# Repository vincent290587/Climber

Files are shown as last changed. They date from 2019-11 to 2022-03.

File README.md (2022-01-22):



# Project

This is another project of an indoor-trainer grade simulator.  
It is meant to be used with Zwift, but could be used with any other similar program or game.  
The concept was inspired by the Wahoo Kickr Climb, but with different strategy / parts !

- [x] Sensors readout
- [x] ANT+ FE-C Slope sniffing
- [x] Kalman filtering
- [x] Actuator command
- [x] User params flash saving
- [x] Zwift TCP packets sniffing for ERG (or any) mode slope sniffing.

<p align="center">
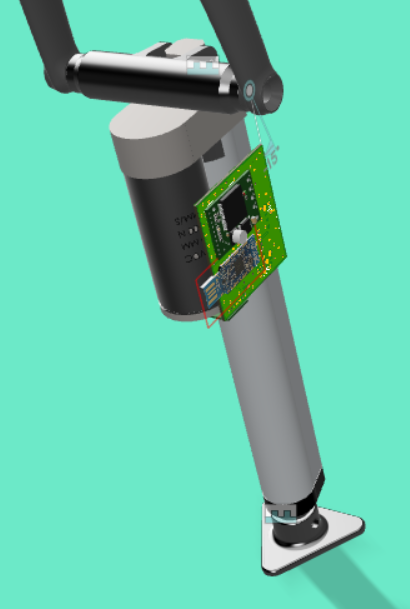
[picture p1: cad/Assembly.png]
Assembly

</p>

# Concept

The ANT+ target incline is sniffed using the ANT+ protocol, it is then compared to the filtered measured front wheel hub height.  
Two 3D printed parts (in the CAD folder) allow to mount securely the actuator to the bike's fork, and to the ground.  
You know the rest ;-)

## Slope detection

The software can work in 2 modes:  
- The slope is sniffed in Zwift TCP packets directly (preferred, but only works with Zwift...),  
- or it can be obtained from the game ANT+ packets (only works in simulation mode and not in ERG...).

So... pick your poison !

## Incline achievement

The current bike front wheel hub's height is computed using a ToF infrared laser sensor: the VL53L1x.  
These measurement are input in a Kalman filter to get a better dynamic estimate of the bike's incline.  
A VNH5019 is then PWMed to drive the linear actuator.

# Hardware

- MCU: nRF52840 (BLE and ANT+), in the form of the PCA10059 (USB dongle) from Nordic
- Incline detection: ToF laser sensor VL53L1x (Pololu)
- Motor controller: VNH5019 (Pololu)

# How to use it ?

## Hardware connections

The pinout that is used is defined in the file named `custom_board_v1.h`.  

Eagle PCB files:

https://github.com/vincent290587/EAGLE/tree/master/Projects/Climber

## Pre-compiled files

See folder /hex.

## Pre-requisites

Download the nRF52 SDK from Nordic:  
https://www.nordicsemi.com/Products/Development-software/nRF5-SDK/Download?lang=en#infotabs  

Decompress it somewhere and write down that location (needed to go in the compil/s340/Makefile.local).

If you choose to use the ANT+ mode you'll have to install the ANT+ keys in that SDK. (follow Nordic's guidelines or take inspiration from https://devzone.nordicsemi.com/f/nordic-q-a/63928/ant-softdevice-integration-into-ant-example-projects-for-nrf5-sdk-17-0-0) 

### To use the BLE mode

#### Preparing the nrf52 PC dongle (AP dongle)

See folder /hex, you can use nRF-Connect to upload the correct softdevice / firmware to the AP dongle.

The AP dongle basically acts as a USB-BLE NUS bridge, scripts in the /zpm folder send the target incline through a COM port,
and the AP dongle forwards the data to the actuator dongle.  

The LED color codes for the AP dongle are the following:
- blinking green: waiting for USB COM port connection (terminal)
- solid green: data is received from the javascript scripts,
- red led: toggled each BLE packet received from the actuator dongle !

#### Preparing the nrf52 actuator dongle

See folder /hex, you can use nRF-Connect to upload the correct softdevice / firmware to the dongle.  

- The red LED indicates the actuator is not being commanded
- The blue LED indicates the actuator is going up
- The green LED indicates the actuator is going down

#### Testing the setup

Test scripts are in the /zpm folder. They use Node.js to run javascript scripts.  
Go to the zpm folder and type `npm install`. The node modules should get installed.  
Open Tester.js and place the correct COM port name.  

You can now run the Tester.js script (`node Tester.js`), which will make your device go up an down every 30 seconds.  
You can use your device with Zwift by typing `node Climber.js` and then starting Zwift as usual.  

#### Getting the slope from Zwift

- First, you will need a working Node.js install. So go to https://nodejs.org/en/download/ and install it,
- Then you need Win10Pcap (if you are under windows), go to http://www.win10pcap.org/download/,
- Finally, go to the `zpm` folder, and open a terminal. Type `npm install` and press enter. The node modules should start getting installed,
- You can now connect your additional dongle. Check which COM port it occupies and fill it in the Climber.js and Tester.js files.

## Building the software

- Go to the compil/s340 folder
- Create a `Makefile.local` file with the path to your SDK and the port used for uploading software to the dongle (You can get inspiration from Makefile.local.sample)
- By default the software will get slope information from a second dongle using BLE, but you can also choose to use the ANT+ packets, and to do so you will have to uncomment the line `#CFLAGS += -DANT_STACK_SUPPORT_REQD` in compil/s340/Makefile. If you are not interested in getting the logs, you might even as well no use BLE at all, and to do so, comment `CFLAGS += -DBLE_STACK_SUPPORT_REQD`.
- Run your favorite `make` command
- Plug your dongle in, and press the little side button to put it in bootloader mode
- Find the name of the dongle port, and make sure it matches the port name given in your `Makefile.local`
- Type `make dfu_softdevice`, which will load the S340 softdevice
- Then type `make dfu`, which will upload the software

The dongle will reboot automagically and it should be running !

### Software editing / tuning

You need a Nordic SDK V15.3 with an equally installed S340 (findable at thisisant.com, and to be put in components/softdevice).
You also need to place the correct ANT / ANT+ keys in your freshly installed SDK ;-)

There are a few parameters you will have to tune to your own setup, although the default values might be ok.  
These are located in the file named `parameters.h`
- `DEFAULT_TARGET_DISTANCE` is the distance measured by the laser sensor when your bike is completely flat (0.0% slope),
- `ACTUATOR_MIN_LENGTH` is the height under which your actuator will never be commanded: aka the low stop,
- `ZWIFT_SLOPE_FACTOR` must be the inverse of Zwift's trainer difficulty.

You will also have to fill in your actuator upward and downward speed in the file `libraries/utils/utils.h` in the function called `map_duty_to_speed`. This is used by the Kalman filter.  
You can use the `Tester.js` script to measure what your actuator can really achieve in terms of speeds, or decide to rely on the datasheet speed of your actuator.

## Full simulation / mock

Yes, the complete system has its own simulator where you can modify settings and look at amazing plots !

!! You need to be using Linux (or WSL on Windows) !!

### Building the simulator

- Go to the TDD folder, and type `cmake ..`
- Then build using `make`
- Run the program `./Climber`

The results are output in a file called `simu.txt`, which you can easily use in a plotting software. (KST plot is warmly recommended, or JSynoptic)

## Using it with Zwift

### If you chose to use ANT+ packets

Congrats ! You are compatible with any training software ! Provided you are using an ANT+ key to connect to your trainer...  
Just power everything up and you should be fine, but one thing to keep in mind: for in Zwift there is a setting called 'trainer difficulty', and it will also reflect on the slope simulated by this device !

For example, if your trainer difficulty is set to 40%, and the current slope in Zwift is 10%, then the device will simulate a 4% incline. Yep.  
To account for this you will have to edit the define `ZWIFT_SLOPE_FACTOR` in `parameters.h`.

### If you chose Zwift TCP packets sniffing (BLE)

Congrats ! You will have the smoothest experience and realistic slope simulation ! But you are only compatile with Zwift...

To be up and running execute the following steps:  
- Follow the pre-requisites to have a working Node.js,
- Plug your second dongle on your computer, its green lights should start blinking,
- Go to the `zpm` folder and open the `Climber.js` file, and change the COM port written in there by the actual COM port of the dongle you just plugged,
- Power the actuator dongle, its light should be solid red,
- The AP dongle red light should start blinking,
- Type in `node Climber.js` in a terminal and press enter,
- You should see logs filling your terminal, which means it is working !

The LED color codes for the actuator dongle are the following:
- red: position stop
- blue / green: going up / down !

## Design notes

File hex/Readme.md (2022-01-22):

# Compiled programs

These files can easily be flash onto a nRF52 dongle using the Nordic nRF-Connect tool.  
Flash the softdevice first and then proceed with the main program file.  

At the end, the flash should look like this in nRF Connect:  

- orange is the official Nordic MBR
- blue is the softdevice
- green is the application
- pink is the official Nordic dongle bootloader

<p align="center">
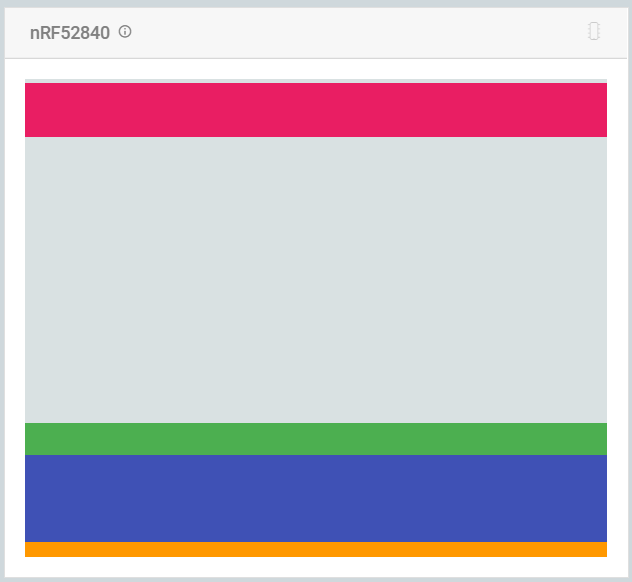
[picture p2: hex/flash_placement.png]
Placement

</p>

## Actuator

### Softdevice

ANT_s340_nrf52840_6.1.1.hex

Available on https://www.thisisant.com/developer/components/nrf52832/#tab_protocol_stacks_tab

### Main program

- Device_ANT.hex for ANT+ mode (only possible if trainer connects using an ANT+ dongle key)
- Device_BLE.hex for BLE mode (needs an AP dongle)

## AP (non ANT+ mode)

### Softdevice

s140_nrf52_7.0.1_softdevice.hex

Available on https://www.nordicsemi.com/Products/Development-software/S140/Download?lang=en#infotabs

### Main program

AP.hex

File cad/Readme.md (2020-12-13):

# Linear actuator mating parts

## Quich release front adapters

- CTop.stl

## 10x100 front adapters

- 10x100_front_adapter.stl

# Smart trainers compatibility

Some smart trainers like the Tacx Neo 2T do not allow rotation on the rear wheel hub because of small teeth in the trainer axle adapters.  
In order to allow rotation without damaging the bike frame, several plastic parts similar to washers are available here:
- Neo2T_Cog-short.stl (Cog side of the trainer)
- Neo2T_Thick long.stl (Other side of the trainer)

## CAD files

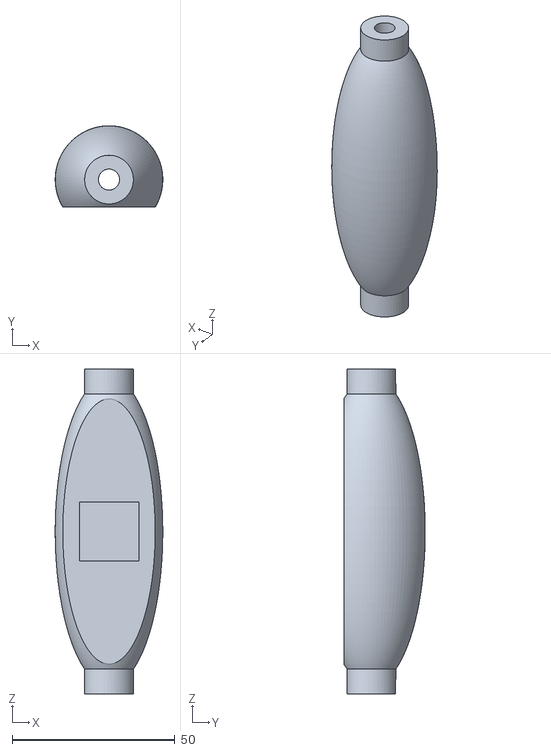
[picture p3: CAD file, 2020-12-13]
cad/CTop.stl
33.1 x 25.1 x 100.0

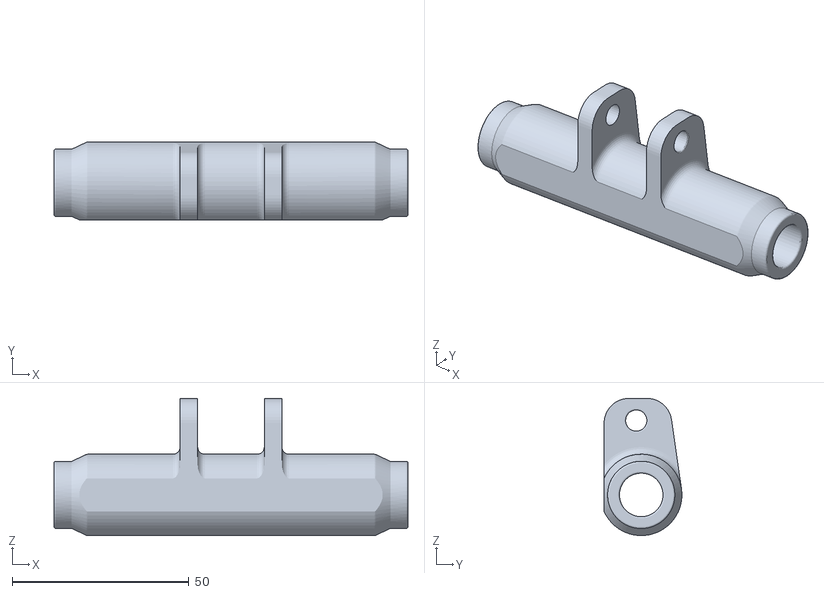
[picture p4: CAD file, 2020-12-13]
cad/10x100_front_adapter.stl
100.0 x 22.0 x 38.7

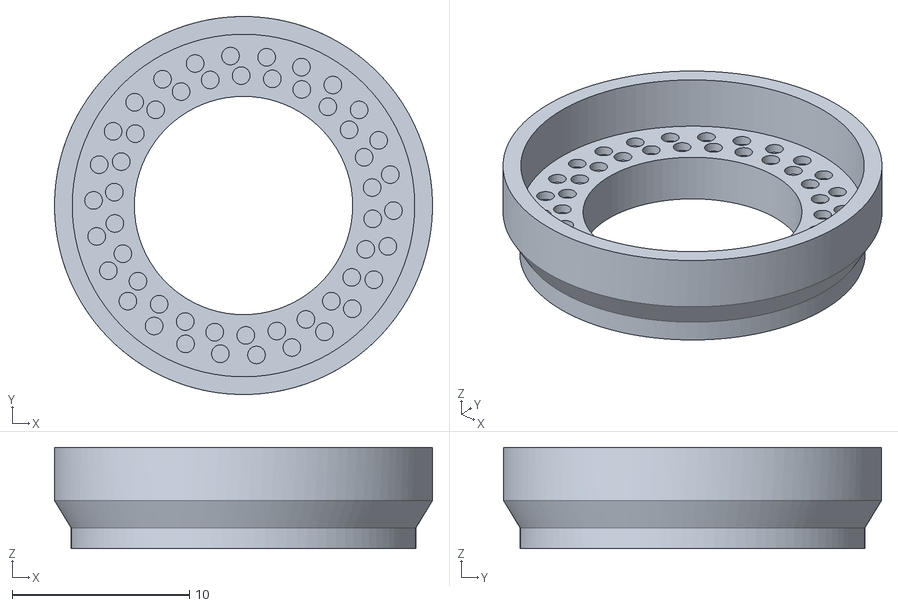
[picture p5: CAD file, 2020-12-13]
cad/Neo2T_Thick-long.stl
21.3 x 21.3 x 5.70

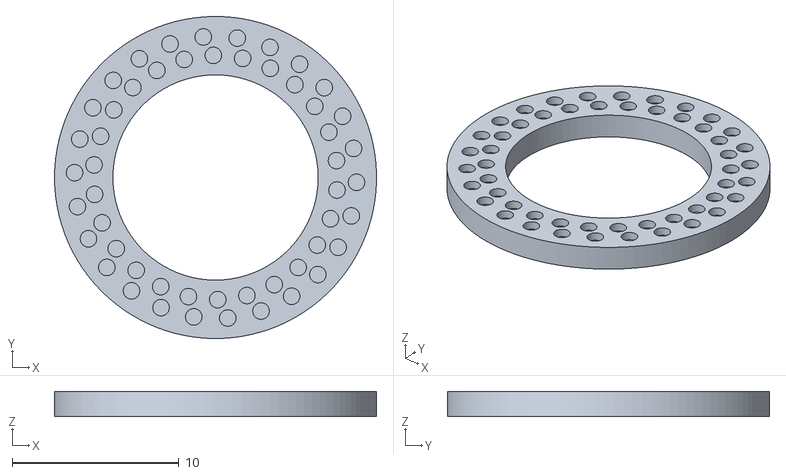
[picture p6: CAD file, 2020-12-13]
cad/Neo2T_Cog-short.stl
19.3 x 19.3 x 1.50

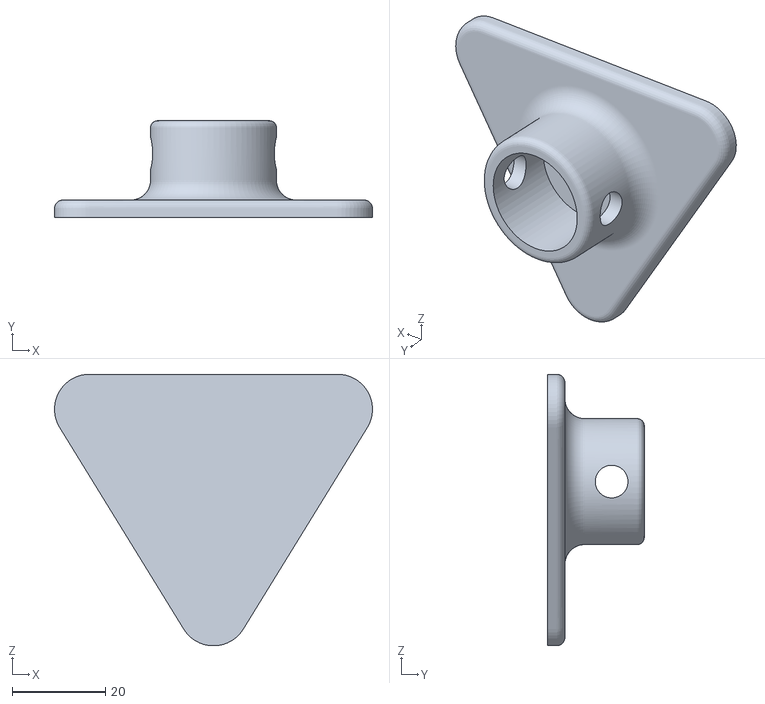
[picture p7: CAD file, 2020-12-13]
cad/CBase.stl
68.1 x 20.7 x 58.2

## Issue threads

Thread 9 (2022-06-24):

Important announcement that may affect your project

luciopaiva, 2022-06-24:
Hey folks,

I'm a backend engineer at [Zwift](https://github.com/zwift) and want to bring to your attention some upcoming changes that are likely to affect your project.

In July we are rolling out a new encryption protocol that will affect all UDP and TCP communication between client and server, and also between client and the Zwift Companion app (ZC), in order to meet a new requirement from Google Play (they recently [changed](https://support.google.com/googleplay/android-developer/answer/10787469) their  user data safety policy).

The rollout will span several days and you may see both encrypted and unencrypted clients running concurrently during that period. It is expected that by July 20th we will have all our communication fully encrypted.

After July 20th, unencrypted clients will be considered deprecated, but still supported. Eventually, however, Zwift will enforce encryption for all clients, but that date is still to be determined.

How exactly that affects your project will depend on what it does:

- **server clones**: they won't be affected by encryption while unencrypted communication is still supported. Encrypted clients must negotiate encryption with the server, and they will simply fall back to unencrypted communication if the server doesn't know any better. When encryption is enforced, however, these projects will stop working;

- **ZC clones**: they won't be affected during that initial phase either. Encrypted clients must also negotiate encryption with ZC, and they will also fall back to unencrypted in case of pre-encryption ZCs. When encryption is enforced, however, these projects will stop working;

- **client sniffers**: those will be immediately impacted when rollout starts. Not only is the protocol specification changing, but the very payload being sniffed by those projects is now encrypted. Logic that relies on reading user data from network packets will simply fail if the data is encrypted, as one would expect;

- **BLE and ANT+ devices**: projects that emulate either BLE or ANT+ devices won't be affected, not even after encryption is enforced (unless of course they also fit any of the roles aforementioned). We are not changing those communication protocols in any way.

Please note that this change is required to secure user data, not to discourage community projects. We are internally discussing if and how we can help community projects go through the change and continue working. That said, please have in mind that this is not merely an engineering decision, but it must also involve other departments like Product and Legal. We will post further updates here as soon as we have any news.

We'll also try our best to answer questions, depending on the availability of our backend engineering team. You can trust replies from any of the engineers listed [here](https://github.com/orgs/zwift/people).

Ride On!

luciopaiva, 2022-06-24:
cc @jeroni7100

This change is directly affecting [zwift-packet-monitor](https://github.com/jeroni7100/zwift-packet-monitor), which is used by Climber. I was going to open an issue there as well, but the Issues section is closed.

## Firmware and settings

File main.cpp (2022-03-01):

/*
 * App.cpp
 *
 *  Created on: 8 oct. 2017
 *      Author: Vincent
 */

#include <stdint.h>
#include <stdio.h>
#include <string.h>

#include <inttypes.h>

#include "hardfault.h"
#include "i2c.h"
#include "helper.h"
#include "ant.h"
#include "bsp.h"
#include "i2c.h"
#include "millis.h"
#include "boards.h"
#include "ble_api_base.h"
#include "app_scheduler.h"
#include "app_timer.h"
#include "nrf_sdm.h"
#include "nrf_strerror.h"
#include "nrf_drv_timer.h"
#include "nrf_drv_clock.h"
#include "task_manager.h"
#include "nrf_bootloader_info.h"
#include "nrfx_wdt.h"
#include "nrf_gpio.h"
#include "nrf_delay.h"
#include "i2c_scheduler.h"
#include "Model.h"
#include "segger_wrapper.h"
#include "WString.h"

#ifdef SOFTDEVICE_PRESENT
#include "nrf_sdh.h"
#endif

#ifdef __cplusplus
extern "C" {
#endif
#include "nrf_pwr_mgmt.h"
#ifdef __cplusplus
}
#endif


#define APP_DELAY           APP_TIMER_TICKS(APP_TIMEOUT_DELAY_MS)

#define SCHED_MAX_EVENT_DATA_SIZE      APP_TIMER_SCHED_EVENT_DATA_SIZE              /**< Maximum size of scheduler events. */
#ifdef SVCALL_AS_NORMAL_FUNCTION
#define SCHED_QUEUE_SIZE               20                                           /**< Maximum number of events in the scheduler queue. More is needed in case of Serialization. */
#else
#define SCHED_QUEUE_SIZE               20                                           /**< Maximum number of events in the scheduler queue. */
#endif

nrfx_wdt_channel_id m_channel_id;

static bsp_event_t m_bsp_evt = BSP_EVENT_NOTHING;

APP_TIMER_DEF(m_job_timer);

/**
 * @brief Handler for timer events.
 */
void timer_event_handler(void* p_context)
{
	W_SYSVIEW_RecordEnterISR();

	if (task_manager_is_started()) {
		task_tick_manage(APP_TIMEOUT_DELAY_MS);
	}

	W_SYSVIEW_RecordExitISR();
}

/**@brief Callback function for asserts in the SoftDevice.
 *
 * @details This function will be called in case of an assert in the SoftDevice.
 *
 * @warning This handler is an example only and does not fit a final product. You need to analyze
 *          how your product is supposed to react in case of Assert.
 * @warning On assert from the SoftDevice, the system can only recover on reset.
 *
 * @param[in] line_num   Line number of the failing ASSERT call.
 * @param[in] file_name  File name of the failing ASSERT call.
 */
extern "C" void assert_nrf_callback(uint16_t line_num, const uint8_t * file_name)
{
	assert_info_t assert_info =
	{
			.line_num    = line_num,
			.p_file_name = file_name,
	};
	app_error_fault_handler(NRF_FAULT_ID_SDK_ASSERT, 0, (uint32_t)(&assert_info));

	LOG_WARNING("System reset");
	LOG_FLUSH();
	NVIC_SystemReset();

	UNUSED_VARIABLE(assert_info);
}

/**
 *
 * @param id
 * @param pc
 * @param info
 */
extern "C" void app_error_fault_handler(uint32_t id, uint32_t pc, uint32_t info)
{
	NRF_LOG_FLUSH();

	m_app_error.err_desc.id = id;
	m_app_error.err_desc.pc = pc;
	m_app_error.err_desc.crc = SYSTEM_DESCR_POS_CRC;

	switch (id)
	{
	case NRF_FAULT_ID_SD_ASSERT:
		NRF_LOG_ERROR("SOFTDEVICE: ASSERTION FAILED");
		break;
	case NRF_FAULT_ID_APP_MEMACC:
		NRF_LOG_ERROR("SOFTDEVICE: INVALID MEMORY ACCESS");
		break;
	case NRF_FAULT_ID_SDK_ASSERT:
	{
		assert_info_t * p_info = (assert_info_t *)info;
		snprintf(m_app_error.err_desc._buffer, sizeof(m_app_error.err_desc._buffer),
				"ASSERTION FAILED at %s : l.%u",
				p_info->p_file_name,
				p_info->line_num);
#if USE_SVIEW
		SEGGER_SYSVIEW_Error(m_app_error.err_desc._buffer);
#else
		NRF_LOG_ERROR(m_app_error.err_desc._buffer);
		LOG_ERROR(m_app_error.err_desc._buffer);
#endif
		break;
	}
	case NRF_FAULT_ID_SDK_ERROR:
	{
		error_info_t * p_info = (error_info_t *)info;
		snprintf(m_app_error.err_desc._buffer, sizeof(m_app_error.err_desc._buffer),
				"ERROR 0x%X [%s] at %s : l.%" PRIu32 "",
				(unsigned int)p_info->err_code,
				nrf_strerror_get(p_info->err_code),
				p_info->p_file_name,
				p_info->line_num);
#if USE_SVIEW
		SEGGER_SYSVIEW_Error(m_app_error.err_desc._buffer);
#else
		NRF_LOG_ERROR("%s", m_app_error.err_desc._buffer);
#endif
		break;
	}
	default:
		NRF_LOG_ERROR("UNKNOWN FAULT at 0x%08X", pc);
		snprintf(m_app_error.err_desc._buffer, sizeof(m_app_error.err_desc._buffer),
				"UNKNOWN FAULT at 0x%08X", (unsigned int)pc);
		break;
	}

	NRF_LOG_FLUSH();

}

extern "C" void app_error_handler(uint32_t error_code, uint32_t line_num, const uint8_t * p_file_name)
{
    NRF_LOG_ERROR("%s : l.%" PRIu32 " code 0x%" PRIX32 "", p_file_name, line_num, error_code);

	NRF_LOG_FLUSH();

	m_app_error.err_desc.id = error_code;
	m_app_error.err_desc.pc = 0;
	m_app_error.err_desc.crc = SYSTEM_DESCR_POS_CRC;

	switch (error_code)
	{
	case NRF_FAULT_ID_SD_ASSERT:
		NRF_LOG_ERROR("SOFTDEVICE: ASSERTION FAILED");
		break;
	case NRF_FAULT_ID_APP_MEMACC:
		NRF_LOG_ERROR("SOFTDEVICE: INVALID MEMORY ACCESS");
		break;
	case NRF_FAULT_ID_SDK_ASSERT:
	{
		snprintf(m_app_error.err_desc._buffer, sizeof(m_app_error.err_desc._buffer),
				"ASSERTION FAILED at %s : l.%" PRIu32 "",
				(const char*)p_file_name,
				line_num);
#if USE_SVIEW
		SEGGER_SYSVIEW_Error(m_app_error.err_desc._buffer);
#else
		NRF_LOG_ERROR(m_app_error.err_desc._buffer);
		LOG_ERROR(m_app_error.err_desc._buffer);
#endif
		break;
	}
	case NRF_FAULT_ID_SDK_ERROR:
	{
		snprintf(m_app_error.err_desc._buffer, sizeof(m_app_error.err_desc._buffer),
				"ERROR 0x%X [%s] at %s : l.%" PRIu32 "",
				(unsigned int)error_code,
				nrf_strerror_get(error_code),
				p_file_name,
				line_num);
#if USE_SVIEW
		SEGGER_SYSVIEW_Error(m_app_error.err_desc._buffer);
#else
		NRF_LOG_ERROR("%s", m_app_error.err_desc._buffer);
#endif
		break;
	}
	default:
		break;
	}

	NRF_LOG_FLUSH();

}

extern "C" void HardFault_process(HardFault_stack_t * p_stack)
{
	NRF_LOG_ERROR("HardFault: pc= %" PRIu32 "", p_stack->pc);
	NRF_LOG_FLUSH();

	m_app_error.hf_desc.crc = SYSTEM_DESCR_POS_CRC;
	memcpy(&m_app_error.hf_desc.stck, p_stack, sizeof(HardFault_stack_t));

	// Restart the system by default
	NVIC_SystemReset();
}

/**@brief Function for initializing the nrf log module.
 */
static void log_init(void)
{
	ret_code_t err_code = NRF_LOG_INIT(NULL);
	APP_ERROR_CHECK(err_code);

	NRF_LOG_DEFAULT_BACKENDS_INIT();

	SVIEW_INIT();
}

/**@brief Interrupt function for handling bsp events.
 */
static void bsp_evt_handler(bsp_event_t evt)
{
	m_bsp_evt = evt;
}

/**@brief Function for handling bsp events.
 */
void bsp_tasks(void)
{
	switch (m_bsp_evt)
	{
	case BSP_EVENT_KEY_0:
	{
		LOG_WARNING("Going to DFU !");
		nrf_pwr_mgmt_shutdown(NRF_PWR_MGMT_SHUTDOWN_GOTO_DFU);
	} break;
	default:
		return; // no implementation needed
	}

	// clear event
	m_bsp_evt = BSP_EVENT_NOTHING;
}

/**@brief Handler for shutdown preparation.
 *
 * @details During shutdown procedures, this function will be called at a 1 second interval
 *          untill the function returns true. When the function returns true, it means that the
 *          app is ready to reset to DFU mode.
 *
 * @param[in]   event   Power manager event.
 *
 * @retval  True if shutdown is allowed by this power manager handler, otherwise false.
 */
static bool app_shutdown_handler(nrf_pwr_mgmt_evt_t event)
{
	ret_code_t err_code;

	switch (event) {
	case NRF_PWR_MGMT_EVT_PREPARE_WAKEUP:
	{
		// TODO prepare wakeup source
	}
	// no break
	case NRF_PWR_MGMT_EVT_PREPARE_SYSOFF:
	{
		LOG_WARNING("Preparing SYSOFF");

		i2c_scheduling_uninit();

//		nrf_gpio_pin_clear(HV_EN);
//		nrf_gpio_pin_set(N_VCCINT_EN);

#if defined (ANT_STACK_SUPPORT_REQD)
	    ant_setup_stop();
#endif

#if defined (BLE_STACK_SUPPORT_REQD)
	    ble_uninit();
#endif

		// Device ready to enter
		err_code = app_timer_stop_all();
		APP_ERROR_CHECK(err_code);

#ifdef SOFTDEVICE_PRESENT
		nrf_sdh_disable_request();
#endif

	} break;
	case NRF_PWR_MGMT_EVT_PREPARE_DFU:
	{
//		nrf_gpio_pin_clear(HV_EN);
//		nrf_gpio_pin_set(N_VCCINT_EN);

#if defined (ANT_STACK_SUPPORT_REQD)
	    ant_setup_stop();
#endif

		err_code = app_timer_stop_all();
		APP_ERROR_CHECK(err_code);

		LOG_WARNING("Power management allowed to reset to DFU mode.");

	} break;
	default:
		break;
	}

	return true;
}

NRF_PWR_MGMT_HANDLER_REGISTER(app_shutdown_handler, 0);


/**
 * @brief WDT events handler.
 */
void wdt_event_handler(void)
{
	//NOTE: The max amount of time we can spend in WDT interrupt is two cycles of 32768[Hz] clock - after that, reset occurs
}


/**@brief Function for initializing buttons and LEDs.
 *
 * @param[out] p_erase_bonds  True if the clear bonds button was pressed to wake the application up.
 */
static void buttons_leds_init(void)
{
	uint32_t err_code = bsp_init(BSP_INIT_BUTTONS | BSP_INIT_LEDS, bsp_evt_handler);
	APP_ERROR_CHECK(err_code);
}

static void pins_init(void)
{
	ret_code_t err_code;

	err_code = nrfx_gpiote_init();
	APP_ERROR_CHECK(err_code);

	// TODO configure pins

	nrf_gpio_cfg_input(LSM6_INT1, NRF_GPIO_PIN_NOPULL);

	nrf_gpio_cfg_input(VL53_INT , NRF_GPIO_PIN_NOPULL);

}

void wdt_reload(void) {
	nrfx_wdt_channel_feed(m_channel_id);
}

void app_shutdown(void) {
	nrf_pwr_mgmt_shutdown(NRF_PWR_MGMT_SHUTDOWN_GOTO_SYSOFF);
}


#ifdef SOFTDEVICE_PRESENT
/**@brief Function for initializing the softdevice
 *
 * @details Initializes the SoftDevice
 */
static void sdh_init(void)
{
	ret_code_t err_code;

	err_code = nrf_sdh_enable_request();
	APP_ERROR_CHECK(err_code);

	ASSERT(nrf_sdh_is_enabled());

}
#endif

/**
 * @brief Function for configuration of REGOUT0 register.
 */
static void vddInit(void)
{
  if (NRF_UICR->REGOUT0 != UICR_REGOUT0_VOUT_3V3)
  {
	NRF_NVMC->CONFIG = NVMC_CONFIG_WEN_Wen << NVMC_CONFIG_WEN_Pos;    //write enable
	while (NRF_NVMC->READY == NVMC_READY_READY_Busy){}
	NRF_UICR->REGOUT0 = UICR_REGOUT0_VOUT_3V3;                        //configurate REGOUT0
	NRF_NVMC->CONFIG = NVMC_CONFIG_WEN_Ren << NVMC_CONFIG_WEN_Pos;
	while (NRF_NVMC->READY == NVMC_READY_READY_Busy){}
        NVIC_SystemReset();                                               // Reset device
  }
}


/**
 *
 * @return 0
 */
int main(void)
{
	ret_code_t err_code;

#ifdef CONFIG_JLINK_MONITOR_ENABLED
	NVIC_SetPriority(DebugMonitor_IRQn, _PRIO_SD_LOW);
	NVIC_ClearPendingIRQ(DebugMonitor_IRQn);
	NVIC_EnableIRQ(DebugMonitor_IRQn);
#warning "!! MONITORING active !!"
#endif

	// Initialize.
	//Configure WDT.
	nrfx_wdt_config_t wdt_config = NRFX_WDT_DEAFULT_CONFIG;
	err_code = nrfx_wdt_init(&wdt_config, wdt_event_handler);
	APP_ERROR_CHECK(err_code);
	err_code = nrfx_wdt_channel_alloc(&m_channel_id);
	APP_ERROR_CHECK(err_code);
	nrfx_wdt_enable();

	vddInit();

	log_init();

#ifdef FPU_INTERRUPT_MODE
	// Enable FPU interrupt
	NVIC_SetPriority(FPU_IRQn, APP_IRQ_PRIORITY_LOWEST);
	NVIC_ClearPendingIRQ(FPU_IRQn);
	NVIC_EnableIRQ(FPU_IRQn);
#endif

	pins_init();

	millis_init();

	LOG_INFO("Init start");

	err_code = app_timer_create(&m_job_timer, APP_TIMER_MODE_REPEATED, timer_event_handler);
	APP_ERROR_CHECK(err_code);

	err_code = app_timer_start(m_job_timer, APP_DELAY, NULL);
	APP_ERROR_CHECK(err_code);

	// check for errors
	if (m_app_error.hf_desc.crc == SYSTEM_DESCR_POS_CRC) {
		LOG_ERROR("Hard Fault found");
		String message = "Hardfault happened: pc = 0x";
		message += String(m_app_error.hf_desc.stck.pc, 16);
		message += " in void ";
		message += m_app_error.void_id;
		LOG_ERROR(message.c_str());
		memset(&m_app_error.hf_desc, 0, sizeof(m_app_error.hf_desc));
	}

	err_code = nrf_pwr_mgmt_init();
	APP_ERROR_CHECK(err_code);

#if APP_SCHEDULER_ENABLED
	APP_SCHED_INIT(SCHED_MAX_EVENT_DATA_SIZE, SCHED_QUEUE_SIZE);
#endif

	buttons_leds_init();
	nrf_gpio_pin_set(LED_1);

	// drivers
	i2c_init();

	// init BLE + ANT
#ifdef SOFTDEVICE_PRESENT
	sdh_init();
#endif
#if defined (ANT_STACK_SUPPORT_REQD)
	ant_stack_init();
	ant_setup_init();
	ant_setup_start();
#endif
#if defined (BLE_STACK_SUPPORT_REQD)
	ble_init();
#endif

	LOG_INFO("App init done");

	NRF_LOG_FLUSH();

	(void)task_create(peripherals_task	, "peripherals_task"	, NULL);
	(void)task_create(sensing_task		, "sensing_task"		, NULL);
	(void)task_create(actuating_task	, "actuating_task"		, NULL);

	// does not return
	task_manager_start(idle_task, NULL);

}

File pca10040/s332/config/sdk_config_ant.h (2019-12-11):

//==========================================================

// <h> nRF_ANT


#ifndef ANT_COMMON_PAGE_71_ENABLED
#define ANT_COMMON_PAGE_71_ENABLED 1
#endif
#if  ANT_COMMON_PAGE_71_ENABLED
#ifndef ANT_COMMON_PAGE_71_LOG_ENABLED
#define ANT_COMMON_PAGE_71_LOG_ENABLED 1
#endif
#if  ANT_COMMON_PAGE_71_LOG_ENABLED
// <o> ANT_COMMON_PAGE_71_LOG_LEVEL  - Default Severity level

// <0=> Off
// <1=> Error
// <2=> Warning
// <3=> Info
// <4=> Debug

#ifndef ANT_COMMON_PAGE_71_LOG_LEVEL
#define ANT_COMMON_PAGE_71_LOG_LEVEL 3
#endif

// <o> ANT_COMMON_PAGE_71_INFO_COLOR  - ANSI escape code prefix.

// <0=> Default
// <1=> Black
// <2=> Red
// <3=> Green
// <4=> Yellow
// <5=> Blue
// <6=> Magenta
// <7=> Cyan
// <8=> White

#ifndef ANT_COMMON_PAGE_71_INFO_COLOR
#define ANT_COMMON_PAGE_71_INFO_COLOR 0
#endif

#endif //ANT_COMMON_PAGE_71_LOG_ENABLED
// </e>

#endif //ANT_COMMON_PAGE_71_ENABLED
// </e>


// <e> ANT_COMMON_PAGE_80_ENABLED - ant_common_page_80 - ANT+ common page 80
//==========================================================
#ifndef ANT_COMMON_PAGE_80_ENABLED
#define ANT_COMMON_PAGE_80_ENABLED 1
#endif
#if  ANT_COMMON_PAGE_80_ENABLED
// <e> ANT_COMMON_PAGE_80_LOG_ENABLED - Enables logging of common page 80 in the module.
//==========================================================
#ifndef ANT_COMMON_PAGE_80_LOG_ENABLED
#define ANT_COMMON_PAGE_80_LOG_ENABLED 1
#endif
#if  ANT_COMMON_PAGE_80_LOG_ENABLED
// <o> ANT_COMMON_PAGE_80_LOG_LEVEL  - Default Severity level

// <0=> Off
// <1=> Error
// <2=> Warning
// <3=> Info
// <4=> Debug

#ifndef ANT_COMMON_PAGE_80_LOG_LEVEL
#define ANT_COMMON_PAGE_80_LOG_LEVEL 3
#endif

// <o> ANT_COMMON_PAGE_80_INFO_COLOR  - ANSI escape code prefix.

// <0=> Default
// <1=> Black
// <2=> Red
// <3=> Green
// <4=> Yellow
// <5=> Blue
// <6=> Magenta
// <7=> Cyan
// <8=> White

#ifndef ANT_COMMON_PAGE_80_INFO_COLOR
#define ANT_COMMON_PAGE_80_INFO_COLOR 0
#endif

#endif //ANT_COMMON_PAGE_80_LOG_ENABLED
// </e>

#endif //ANT_COMMON_PAGE_80_ENABLED
// </e>

// <e> ANT_COMMON_PAGE_81_ENABLED - ant_common_page_81 - ANT+ common page 81
//==========================================================
#ifndef ANT_COMMON_PAGE_81_ENABLED
#define ANT_COMMON_PAGE_81_ENABLED 1
#endif
#if  ANT_COMMON_PAGE_81_ENABLED
// <e> ANT_COMMON_PAGE_81_LOG_ENABLED - Enables logging of common page 81 in the module.
//==========================================================
#ifndef ANT_COMMON_PAGE_81_LOG_ENABLED
#define ANT_COMMON_PAGE_81_LOG_ENABLED 1
#endif
#if  ANT_COMMON_PAGE_81_LOG_ENABLED
// <o> ANT_COMMON_PAGE_81_LOG_LEVEL  - Default Severity level

// <0=> Off
// <1=> Error
// <2=> Warning
// <3=> Info
// <4=> Debug

#ifndef ANT_COMMON_PAGE_81_LOG_LEVEL
#define ANT_COMMON_PAGE_81_LOG_LEVEL 3
#endif

// <o> ANT_COMMON_PAGE_81_INFO_COLOR  - ANSI escape code prefix.

// <0=> Default
// <1=> Black
// <2=> Red
// <3=> Green
// <4=> Yellow
// <5=> Blue
// <6=> Magenta
// <7=> Cyan
// <8=> White

#ifndef ANT_COMMON_PAGE_81_INFO_COLOR
#define ANT_COMMON_PAGE_81_INFO_COLOR 0
#endif

#endif //ANT_COMMON_PAGE_81_LOG_ENABLED
// </e>

#endif //ANT_COMMON_PAGE_81_ENABLED
// </e>



//==========================================================
// <e> ANT_FEC_ENABLED - ant_bpwr - Bicycle Power Profile
//==========================================================
#ifndef ANT_FEC_ENABLED
#define ANT_FEC_ENABLED 1
#endif
#if  ANT_FEC_ENABLED
// <e> ANT_FEC_LOG_ENABLED - Enables general logging in the module.
//==========================================================
#ifndef ANT_FEC_LOG_ENABLED
#define ANT_FEC_LOG_ENABLED 1
#endif
#if  ANT_FEC_LOG_ENABLED
// <o> ANT_FEC_LOG_LEVEL  - Default Severity level

// <0=> Off
// <1=> Error
// <2=> Warning
// <3=> Info
// <4=> Debug

#ifndef ANT_FEC_LOG_LEVEL
#define ANT_FEC_LOG_LEVEL 0
#endif

// <o> ANT_FEC_INFO_COLOR  - ANSI escape code prefix.

// <0=> Default
// <1=> Black
// <2=> Red
// <3=> Green
// <4=> Yellow
// <5=> Blue
// <6=> Magenta
// <7=> Cyan
// <8=> White

#ifndef ANT_FEC_INFO_COLOR
#define ANT_FEC_INFO_COLOR 0
#endif

#endif //ANT_FEC_LOG_ENABLED
// </e>

// <e> ANT_FEC_COMMON_LOG_ENABLED - Enables logging of FEC tracing common data.
//==========================================================
#ifndef ANT_FEC_COMMON_LOG_ENABLED
#define ANT_FEC_COMMON_LOG_ENABLED 0
#endif
#if  ANT_FEC_COMMON_LOG_ENABLED
// <o> ANT_FEC_COMMON_LOG_LEVEL  - Default Severity level

// <0=> Off
// <1=> Error
// <2=> Warning
// <3=> Info
// <4=> Debug

#ifndef ANT_FEC_COMMON_LOG_LEVEL
#define ANT_FEC_COMMON_LOG_LEVEL 3
#endif

// <o> ANT_FEC_COMMON_INFO_COLOR  - ANSI escape code prefix.

// <0=> Default
// <1=> Black
// <2=> Red
// <3=> Green
// <4=> Yellow
// <5=> Blue
// <6=> Magenta
// <7=> Cyan
// <8=> White

#ifndef ANT_FEC_COMMON_INFO_COLOR
#define ANT_FEC_COMMON_INFO_COLOR 0
#endif

#endif //ANT_FEC_COMMON_LOG_ENABLED
// </e>

#ifndef ANT_FEC_PAGE_2_LOG_ENABLED
#define ANT_FEC_PAGE_2_LOG_ENABLED 0
#endif
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

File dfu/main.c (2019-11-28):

/**
 * Copyright (c) 2016 - 2019, Nordic Semiconductor ASA
 *
 * All rights reserved.
 *
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
 * 3. Neither the name of Nordic Semiconductor ASA nor the names of its
 *    contributors may be used to endorse or promote products derived from this
 *    software without specific prior written permission.
 *
 * 4. This software, with or without modification, must only be used with a
 *    Nordic Semiconductor ASA integrated circuit.
 *
 * 5. Any software provided in binary form under this license must not be reverse
 *    engineered, decompiled, modified and/or disassembled.
 *
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
 */
/** @file
 *
 * @defgroup bootloader_secure_ble main.c
 * @{
 * @ingroup dfu_bootloader_api
 * @brief Bootloader project main file for secure DFU.
 *
 */

#include <stdint.h>
#include "boards.h"
#include "nrf_mbr.h"
#include "nrf_bootloader.h"
#include "nrf_bootloader_app_start.h"
#include "nrf_bootloader_dfu_timers.h"
#include "nrf_dfu.h"
#include "nrf_log.h"
#include "nrf_log_ctrl.h"
#include "nrf_log_default_backends.h"
#include "app_error.h"
#include "app_error_weak.h"
#include "nrf_bootloader_info.h"
#include "nrf_delay.h"

static void on_error(void)
{
    NRF_LOG_FINAL_FLUSH();

#if NRF_MODULE_ENABLED(NRF_LOG_BACKEND_RTT)
    // To allow the buffer to be flushed by the host.
    nrf_delay_ms(100);
#endif
#ifdef NRF_DFU_DEBUG_VERSION
    NRF_BREAKPOINT_COND;
#endif
    NVIC_SystemReset();
}


void app_error_handler(uint32_t error_code, uint32_t line_num, const uint8_t * p_file_name)
{
    NRF_LOG_ERROR("%s:%d", p_file_name, line_num);
    on_error();
}


void app_error_fault_handler(uint32_t id, uint32_t pc, uint32_t info)
{
    NRF_LOG_ERROR("Received a fault! id: 0x%08x, pc: 0x%08x, info: 0x%08x", id, pc, info);
    on_error();
}


void app_error_handler_bare(uint32_t error_code)
{
    NRF_LOG_ERROR("Received an error: 0x%08x!", error_code);
    on_error();
}

/**
 * @brief Function notifies certain events in DFU process.
 */
static void dfu_observer(nrf_dfu_evt_type_t evt_type)
{
    switch (evt_type)
    {
        case NRF_DFU_EVT_DFU_FAILED:
        case NRF_DFU_EVT_DFU_ABORTED:
        case NRF_DFU_EVT_DFU_INITIALIZED:
            bsp_board_init(BSP_INIT_LEDS);
//            bsp_board_led_on(BSP_BOARD_LED_0);
//            bsp_board_led_on(BSP_BOARD_LED_1);
//            bsp_board_led_off(BSP_BOARD_LED_2);
            break;
        case NRF_DFU_EVT_TRANSPORT_ACTIVATED:
            bsp_board_led_on(BSP_BOARD_LED_0);
            break;
        case NRF_DFU_EVT_DFU_STARTED:
            break;
        default:
            break;
    }
}


/**@brief Function for application main entry. */
int main(void)
{
    uint32_t ret_val;

    // Protect MBR and bootloader code from being overwritten.
    ret_val = nrf_bootloader_flash_protect(0, MBR_SIZE, false);
    APP_ERROR_CHECK(ret_val);
    ret_val = nrf_bootloader_flash_protect(BOOTLOADER_START_ADDR, BOOTLOADER_SIZE, false);
    APP_ERROR_CHECK(ret_val);

    (void) NRF_LOG_INIT(nrf_bootloader_dfu_timer_counter_get);
    NRF_LOG_DEFAULT_BACKENDS_INIT();

    NRF_LOG_INFO("Inside main");

    ret_val = nrf_bootloader_init(dfu_observer);
    APP_ERROR_CHECK(ret_val);

    // Either there was no DFU functionality enabled in this project or the DFU module detected
    // no ongoing DFU operation and found a valid main application.
    // Boot the main application.
    nrf_bootloader_app_start();

    // Should never be reached.
    NRF_LOG_INFO("After main");
}

/**
 * @}
 */

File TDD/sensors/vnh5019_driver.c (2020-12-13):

/*
 * vnh5019_driver.c
 *
 *  Created on: 28 nov. 2019
 *      Author: Vincent
 */

#include <stdint.h>
#include "gpio.h"
#include "utils.h"
#include "boards.h"
#include "millis.h"
#include "helper.h"
#include "segger_wrapper.h"
#include "vnh5019_driver.h"


int16_t m_vnh_duty_cycle = 0;
uint32_t m_calc_last_time = 0;
float m_vnh_speed_mm_s = 0.0f;

static float m_sim_length = 25;
static int m_is_blocked = 0;

int16_t tdd_vnh5019_driver__get_length(void) {

	// map actuator speed to command
	m_vnh_speed_mm_s = map_duty_to_speed(m_vnh_duty_cycle);

	float delta = (float)m_vnh_speed_mm_s * (float)(millis() - m_calc_last_time) / 1000.0f;

	if (m_sim_length + delta > 200) {
		m_sim_length = 200;
		m_is_blocked = 1;
	} else
	if (m_sim_length + delta <   0) {
		m_sim_length = 0;
		m_is_blocked = 1;
	} else {
		m_sim_length += delta;
		m_is_blocked = 0;
	}

	m_calc_last_time = millis();

	return (int16_t)m_sim_length + 300;
}

void vnh5019_driver__init(void) {

	w_task_delay(40);
}

uint16_t vnh5019_driver__setM1_duty(int16_t s_duty_cycle, uint8_t force)
{
	m_vnh_duty_cycle = s_duty_cycle;

	uint16_t res = 0;
	if (s_duty_cycle < 0)
	{
		res = -s_duty_cycle;
	} else {
		res = s_duty_cycle;
	}

	return res;
}

int16_t vnh5019_driver__getM1_duty(void)
{
	return m_vnh_duty_cycle;
}

void vnh5019_driver__setM1Brake(uint16_t brake)
{

}

// Return motor 1 current value in milliamps.
int32_t vnh5019_driver__getM1CurrentMilliamps(void)
{
	if (!m_is_blocked && (m_vnh_duty_cycle <= -1 || m_vnh_duty_cycle > 7)) return 2500;
	return -200;
}

// Return error status for motor 1
uint32_t vnh5019_driver__getM1Fault(void)
{
	return !gpio_get(VNH_DIAG1);
}

void vnh5019_driver__tasks(void) {


}

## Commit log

2019-11-28 VNH5019 driver
2019-12-01 New board
2019-12-04 pwm works
2019-12-11 Added calibration
2019-12-12 A bit of work on jlink monitoring Removed unused filter
2019-12-15 New board def
2019-12-15 New PWM duty cycling Cleanup
2019-12-17 Safer kalman filter with FPE
2019-12-18 Added pca10040 board for debugging
2019-12-18 Fixed the ERG fix
    [Simulator.cpp, data_dispatcher.cpp]
2019-12-19 Fixed simulator and filter command
    [Simulator.cpp, data_dispatcher.cpp]
2019-12-19 SPlit Kalman filters
2019-12-19 Changed gains and important simulation things (noise)
    [Simulator.cpp, data_dispatcher.cpp, vnh5019_driver.c]
2019-12-20 Bug in ZPM decoder
    [Simulator.cpp]
2019-12-28 Added PID control !
2019-12-28 PID setting actuator smart stop PWM overflow bug
    [data_dispatcher.cpp, vnh5019_driver.c]
2019-12-29 Changed PID setting
2019-12-29 Attempt at detecting actuator end of course
2019-12-29 More filtering on the slope commands
2020-01-07 Added PWM duty force
2020-01-25 Solved the "getting stuck" bug Solved the "rapid direction inversion" bug
    [data_dispatcher.cpp]
2020-01-28 Added BLE NUS logging for errors
    [data_dispatcher.cpp]
2020-01-30 Better motor handling
2020-01-30 Weird error flag !!
    [helper.c]
2020-01-31 Moved PWM code
2020-01-31 Direct PWM driver
2020-02-01 New PWM now works !
2020-02-07 Added 3D files
    [CBase.stl, CTop.stl]
2020-02-07 Added CAD picture
2020-02-25 Bug in CRC and user settings
    [Simulator.cpp, data_dispatcher.cpp, fram.c]
2020-02-25 Fix for new nRFX PWM driver
    [sdk_config.h]
2020-04-21 Added new CAD files
    [10x100_front_adapter.stl, Neo2T_Cog-short.stl, Neo2T_Thick-long.stl]
2022-03-01 Fixed dongle external regulator
    [main.cpp]
